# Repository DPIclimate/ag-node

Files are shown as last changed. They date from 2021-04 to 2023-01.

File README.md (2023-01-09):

<h2 align="center">
    Agriculture Node
</h2>
<p align="center">
  <a href="#about">About</a> •
  <a href="#schematic">Schematic</a> •
  <a href="#protocol / algorithm">Protocol</a> •
  <a href="#firmware docs">Docs</a> •
  <a href="#license">License</a>
</p>

<p align="center">
  <a href="https://dpiclimate.github.io/ag-node">
    
  </a>
</p>



## About

The agriculture node (ag-node) is an automatic multi-weigh-station for measuring the live-weight of sheep  in remote locations. The station can be situated against a trough for which sheep weights will be recorded as they access feed or water. An in-built LoRaWAN radio sends data (containing live-weight information) back to a local gateway and onto the end user. Additional interfaces are provided, including; SDI-12, I<sub>2</sub>C and OneWire to allow for various sensors to be connected to the device (such as trough level sensors, temperature monitors etc.).

## Schematic

The devices schematic can be found at: [schematic.pdf](https://github.com/DPIclimate/ag-node/blob/master/figures/schematic.pdf)

Basic components are summarised in the below image. Where A is the analog-to-digital converter, B is the LoRaWAN communication infrastructure and C is the peripheral sensor connectors (I<sub>2</sub>C, OneWire and SDI-12).

<div align="middle"> 
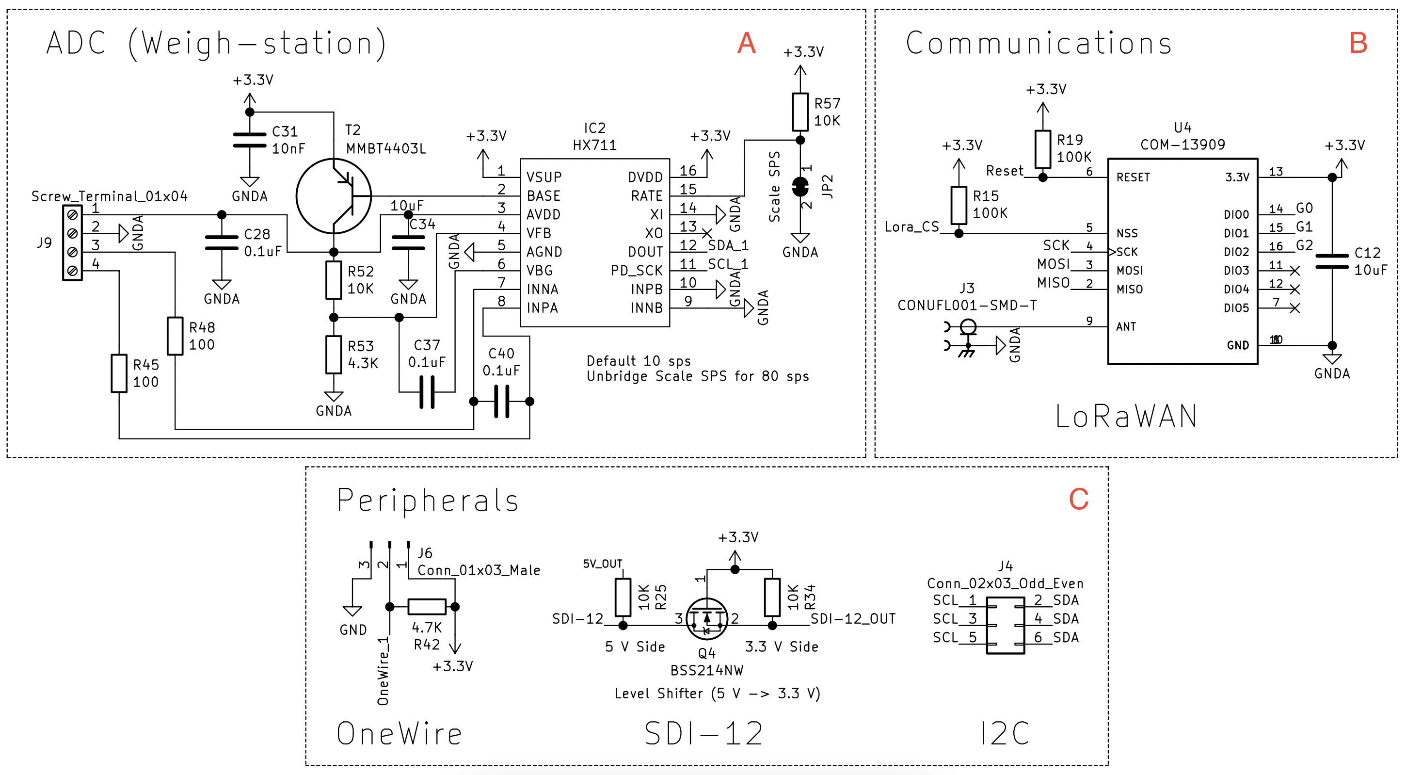
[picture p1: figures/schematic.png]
	
</div>

## Protocol / Algorithm

As the device operates autonomously (sheep are weighed in an unsupervised manner) an algorithm to capture the maximum stable weight (and an error representation) is provided.

The protocol is explained below and a visual representation is provided.

1. A weight is captured (triggered by a sheep stepping on a scale) consisting of a time-series of weights while the sheep is on the platform

2. This time-series data is sliced into groups of 5 values

3. The slope between the first and last value is calculated (where values < 0.1) are discarded as they represent unstable weights

4. The Root Mean Square Error (RMSE) of the fitted line is calculated

5. The average of the 5 points are taken

6. An evaluation of the new weight is made against previous slices (see figure below under the Method `Evaluate` for an equation that represents this)

<div align="middle"> 
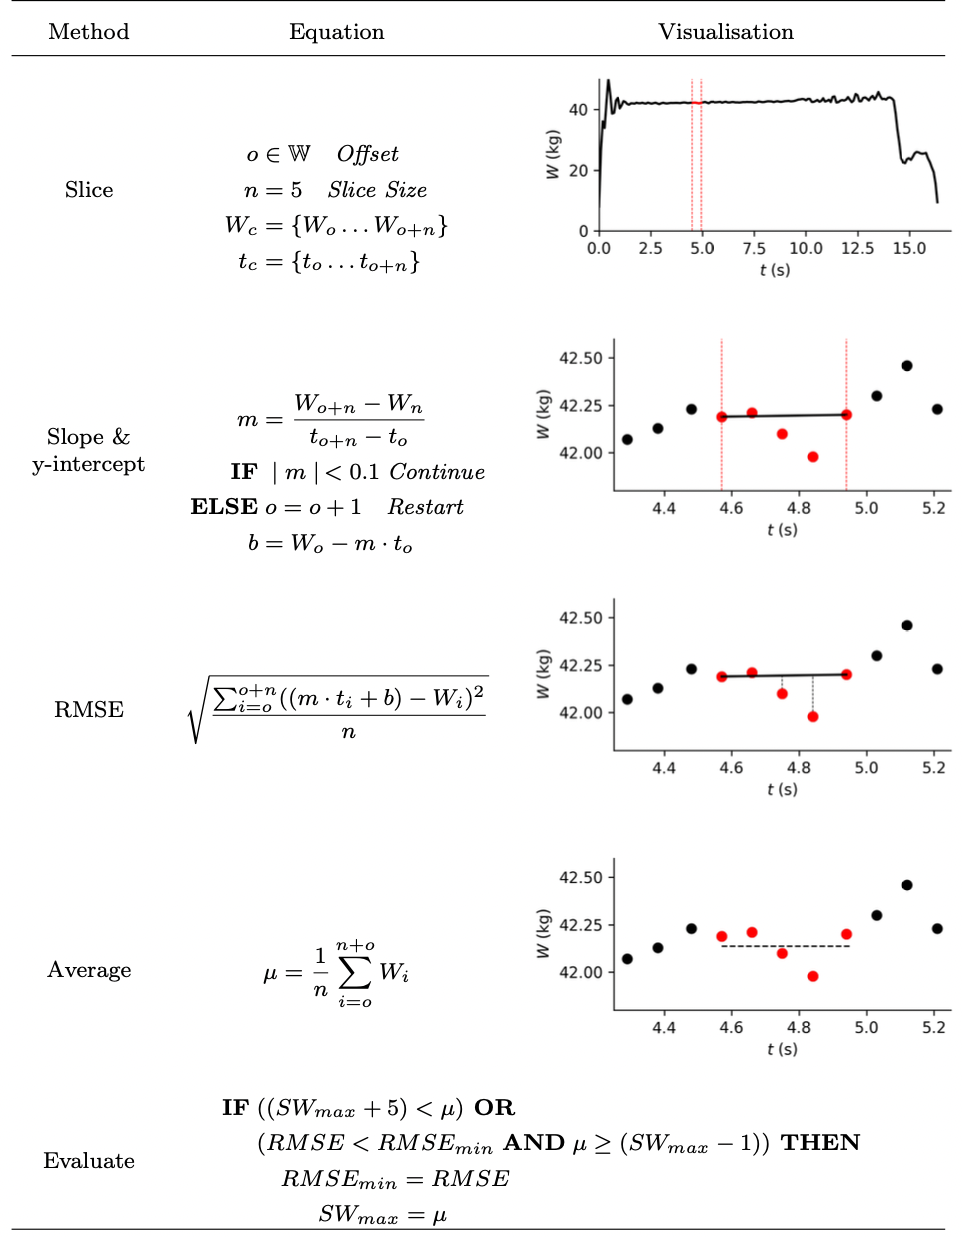
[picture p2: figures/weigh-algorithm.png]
	
</div>

## Firmware Docs

Firmware documentation can be found [here](https://dpiclimate.github.io/ag-node)

An illustration of the devices operations can be found below:

<div align="middle"> 
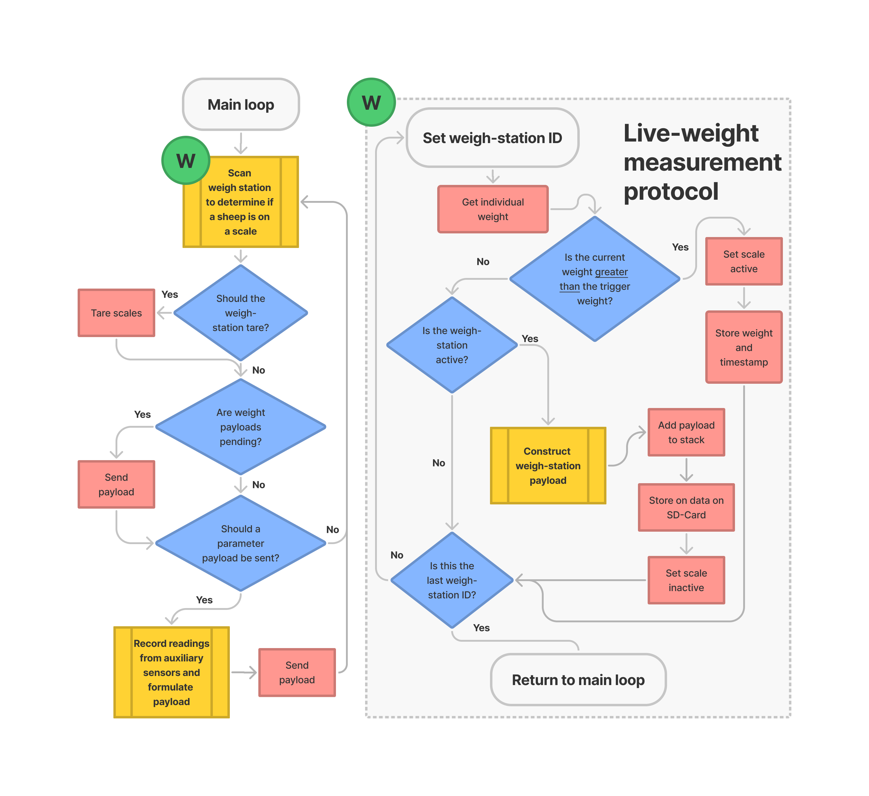
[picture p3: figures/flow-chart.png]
	
</div>

## License

Ag-node is MIT licensed, as found in the [LICENSE](https://github.com/DPIclimate/ag-node/blob/master/LICENSE) file.

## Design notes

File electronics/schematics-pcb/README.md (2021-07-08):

## Version 0.3
- Uses Teensy 3.6 as mainboard controller (run at a low clock speed) and defaults to sleep
- Has 3 weigh station ports (controlled by a HX711 and a ATMega328) 
- ATMega328's have interrupts connected to the teensy to wake it up when they want to transfer some data (over I2C)
- Single lorawan module (connected to teensy, can sleep when not in use)
- Designed to be a low-power device with multiple processors for asynchronous readings

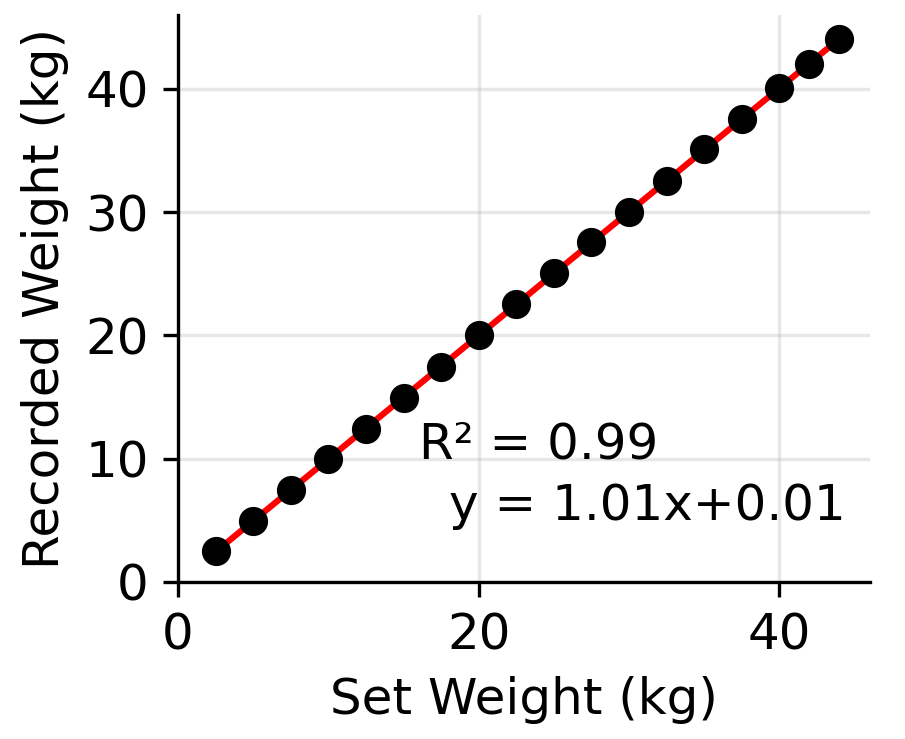
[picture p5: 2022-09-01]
figures/linearity.png

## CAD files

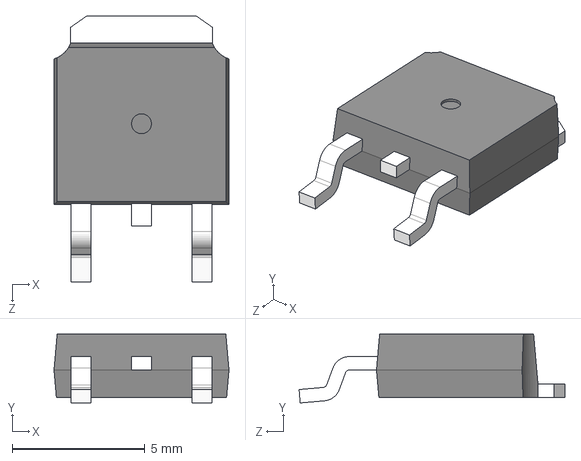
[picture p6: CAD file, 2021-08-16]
electronics/additionalParts/AOD417/AOD417.step
6.60 x 2.60 x 10.0 mm

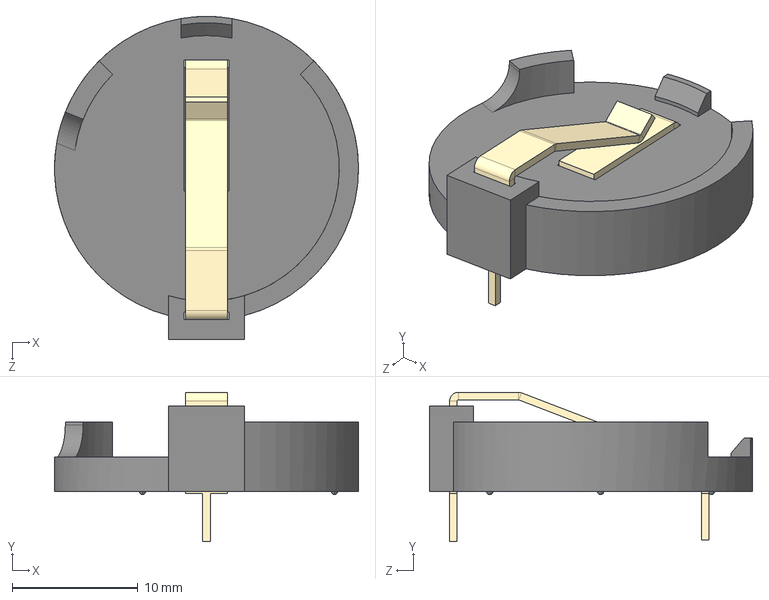
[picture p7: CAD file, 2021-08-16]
electronics/additionalParts/BH32T-C-G/BH32T-C-G.step
24.1 x 11.9 x 25.7 mm

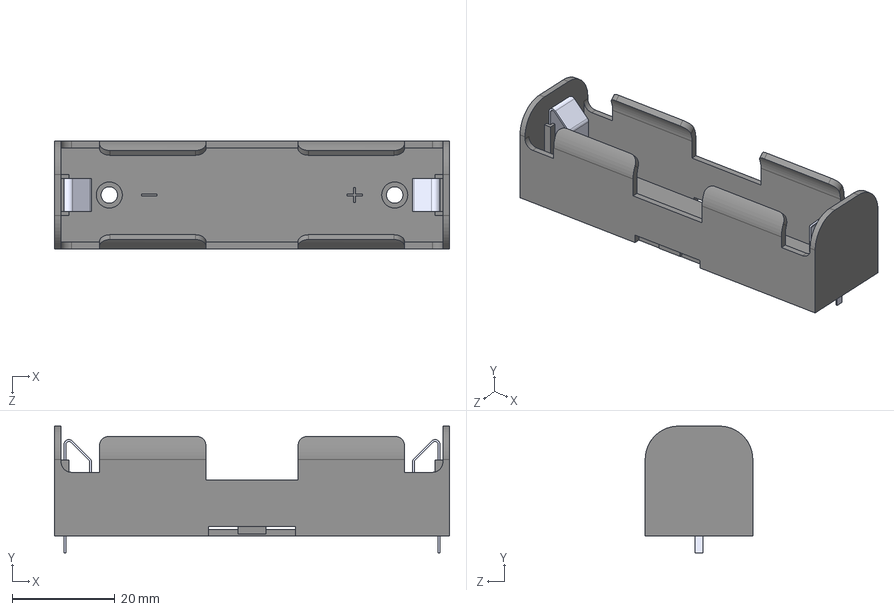
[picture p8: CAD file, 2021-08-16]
electronics/additionalParts/BK-18650-PC2/BK-18650-PC2.step
77.0 x 24.7 x 21.0 mm

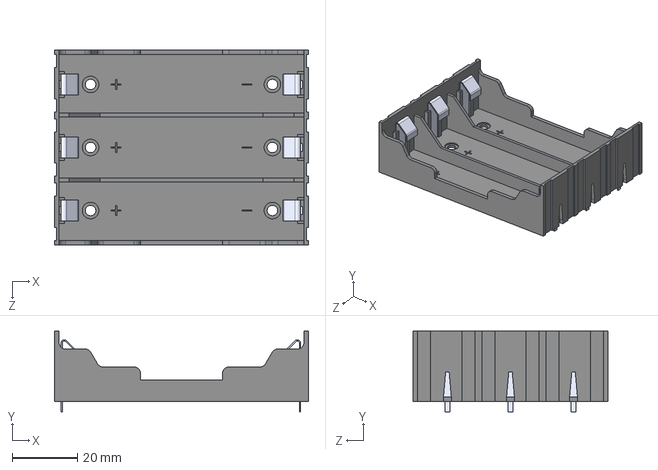
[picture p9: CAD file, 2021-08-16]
electronics/additionalParts/BK-18650-PC6/BK-18650-PC6.step
77.7 x 24.7 x 59.7 mm

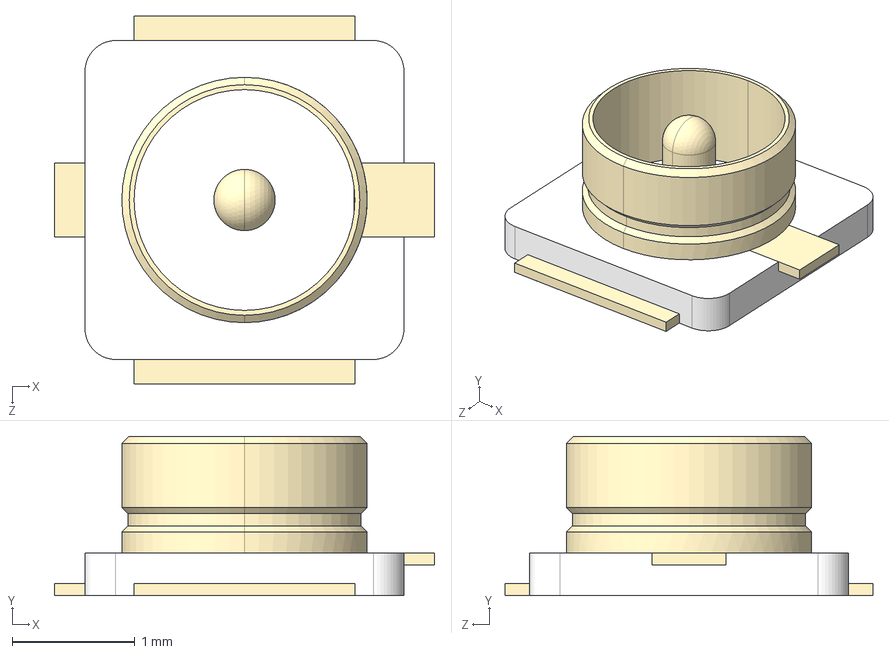
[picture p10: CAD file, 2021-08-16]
electronics/additionalParts/CONUFL001-SMD-T/CONUFL001-SMD-T.step
3.10 x 1.30 x 3.00 mm

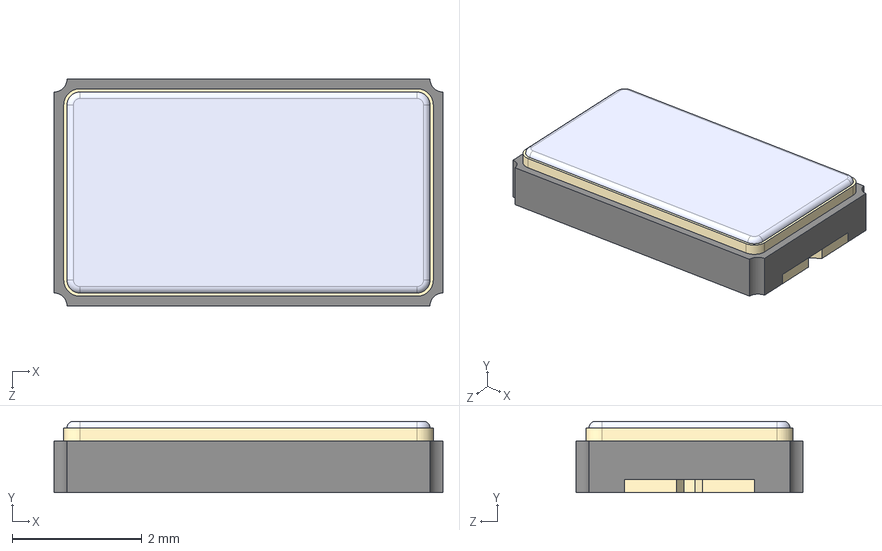
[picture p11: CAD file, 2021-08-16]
electronics/additionalParts/ECS-200-20-23A-EN-TR/ECS-200-20-23A-EN-TR.step
6.00 x 1.10 x 3.50 mm

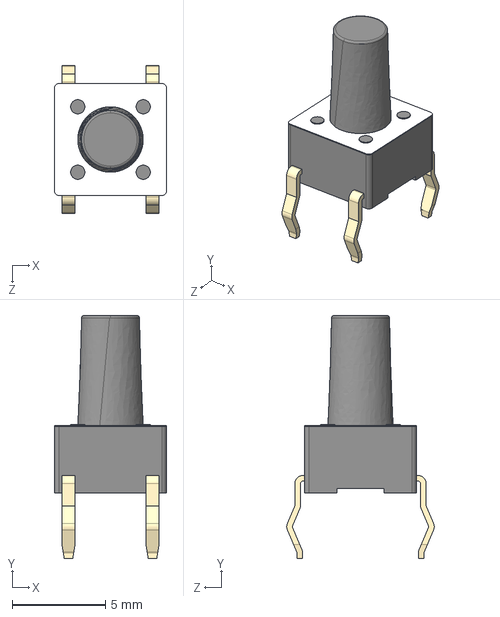
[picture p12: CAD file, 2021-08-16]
electronics/additionalParts/FSM8JH/FSM8JH.step
5.99 x 13.0 x 7.90 mm

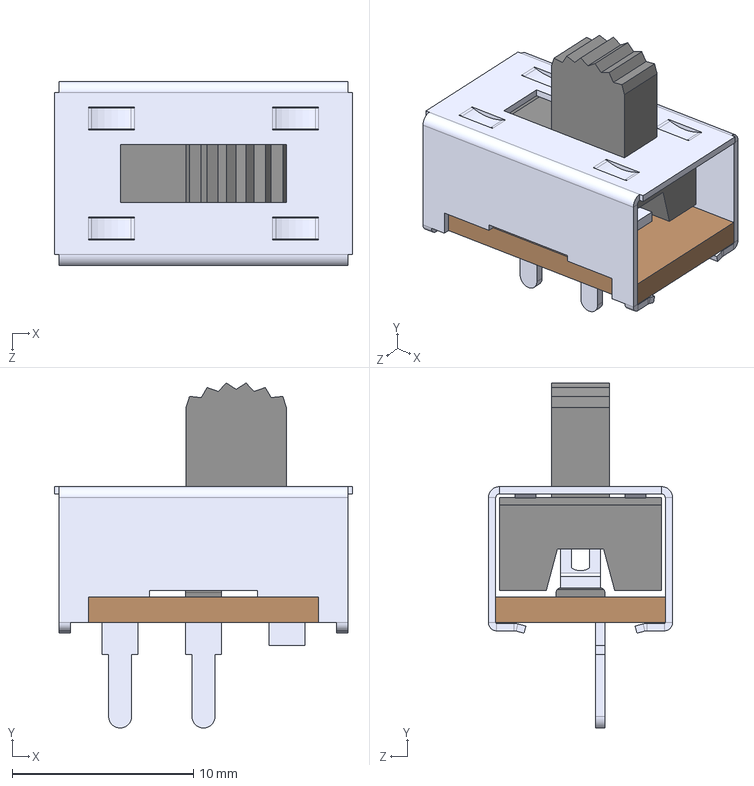
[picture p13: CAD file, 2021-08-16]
electronics/additionalParts/GF-123-0054/GF-123-0054.step
16.5 x 19.0 x 10.2 mm

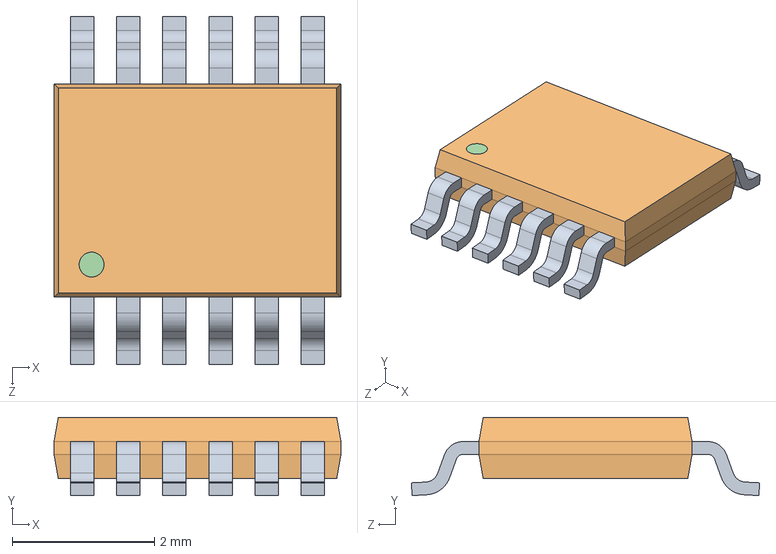
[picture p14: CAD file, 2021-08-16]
electronics/additionalParts/LT3652IMSETRPBF/LT3652IMSETRPBF.step
4.04 x 1.10 x 4.90 mm

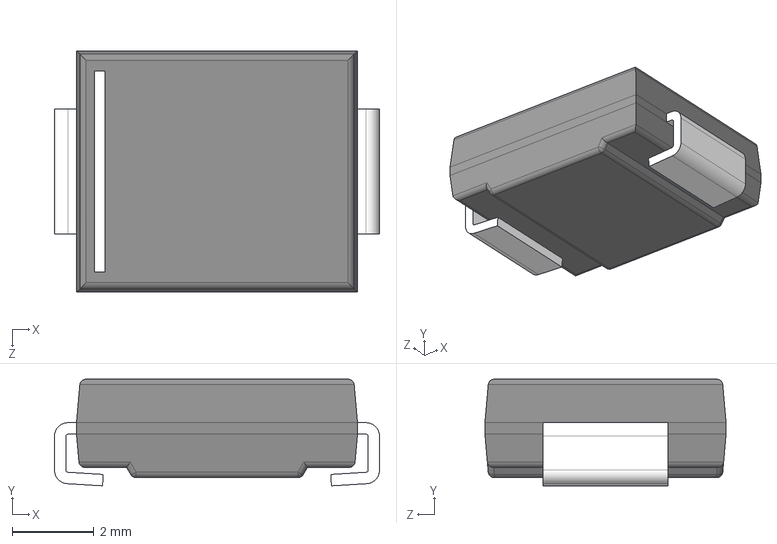
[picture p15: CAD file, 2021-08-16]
electronics/additionalParts/MBRS340/MBRS340.step
7.95 x 2.61 x 5.90 mm

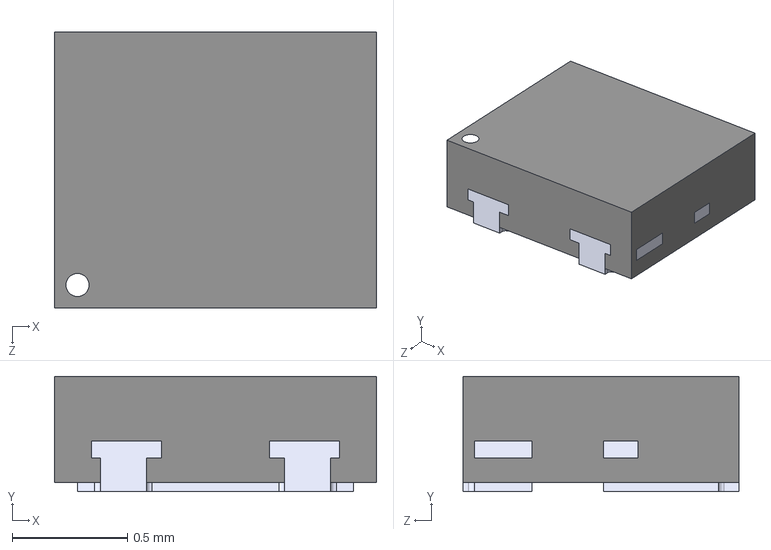
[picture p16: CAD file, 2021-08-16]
electronics/additionalParts/MMBT4403L/MMBT4403L.step
1.40 x 0.5 x 1.20 mm

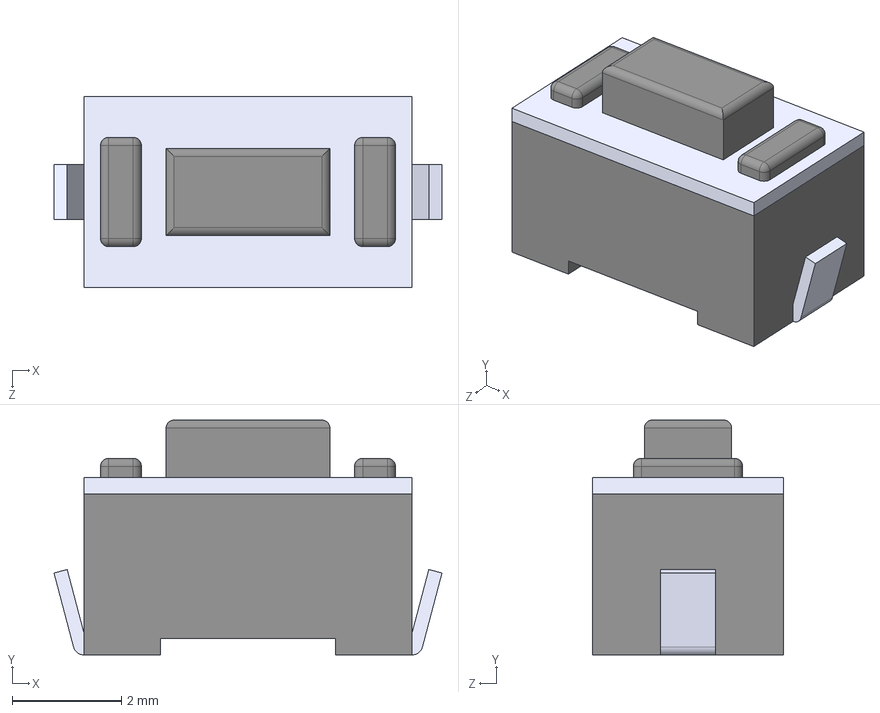
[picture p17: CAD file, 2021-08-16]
electronics/additionalParts/PTS636_SM43J_SMTR_LFS/PTS636_SM43J_SMTR_LFS.step
7.10 x 4.30 x 3.50 mm

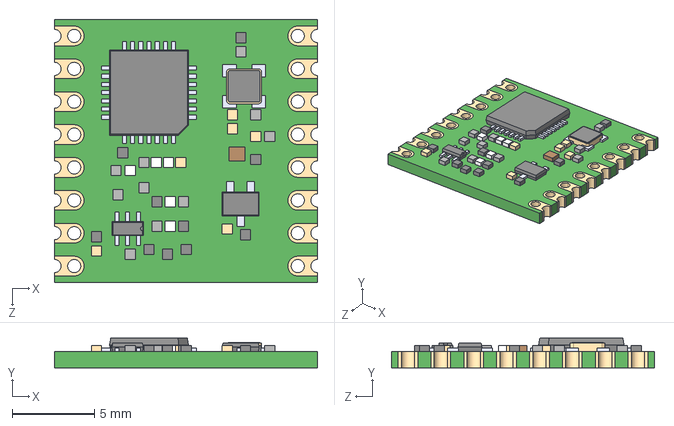
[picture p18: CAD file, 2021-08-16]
electronics/additionalParts/RFM69HCW/COM-13909.step
16.0 x 1.80 x 16.0 mm

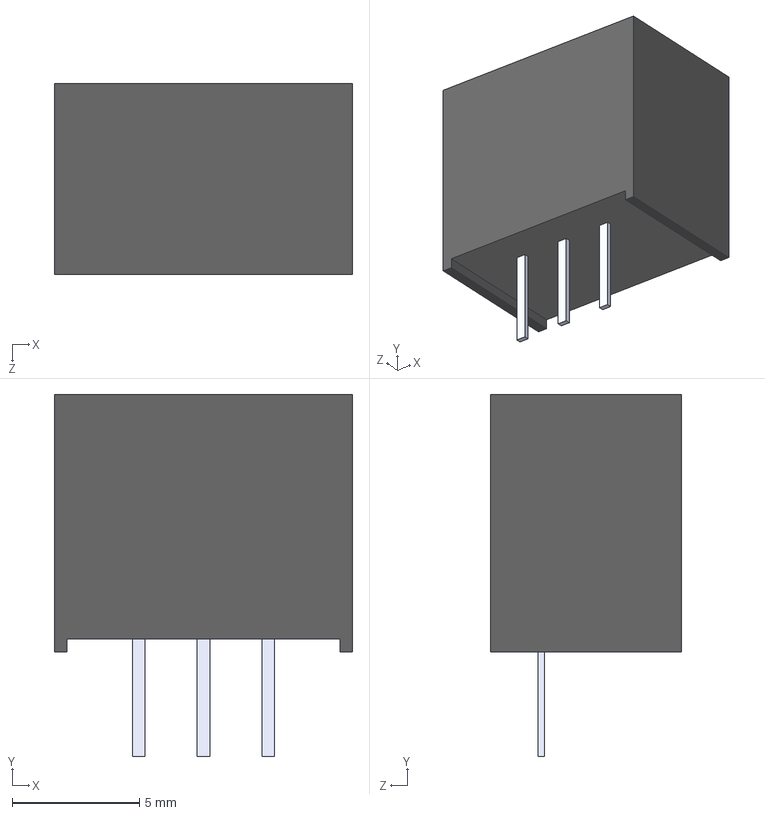
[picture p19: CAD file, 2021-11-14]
electronics/additionalParts/TSR_1-2450/TSR_1-2450.step
11.7 x 14.2 x 7.50 mm

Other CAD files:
electronics/additionalParts/TXB0104D/TXB0104D.step
electronics/additionalParts/L101011MS02Q/L101011MS02Q.step
electronics/additionalParts/TPS73633DBVT/TPS73633DBVT.step

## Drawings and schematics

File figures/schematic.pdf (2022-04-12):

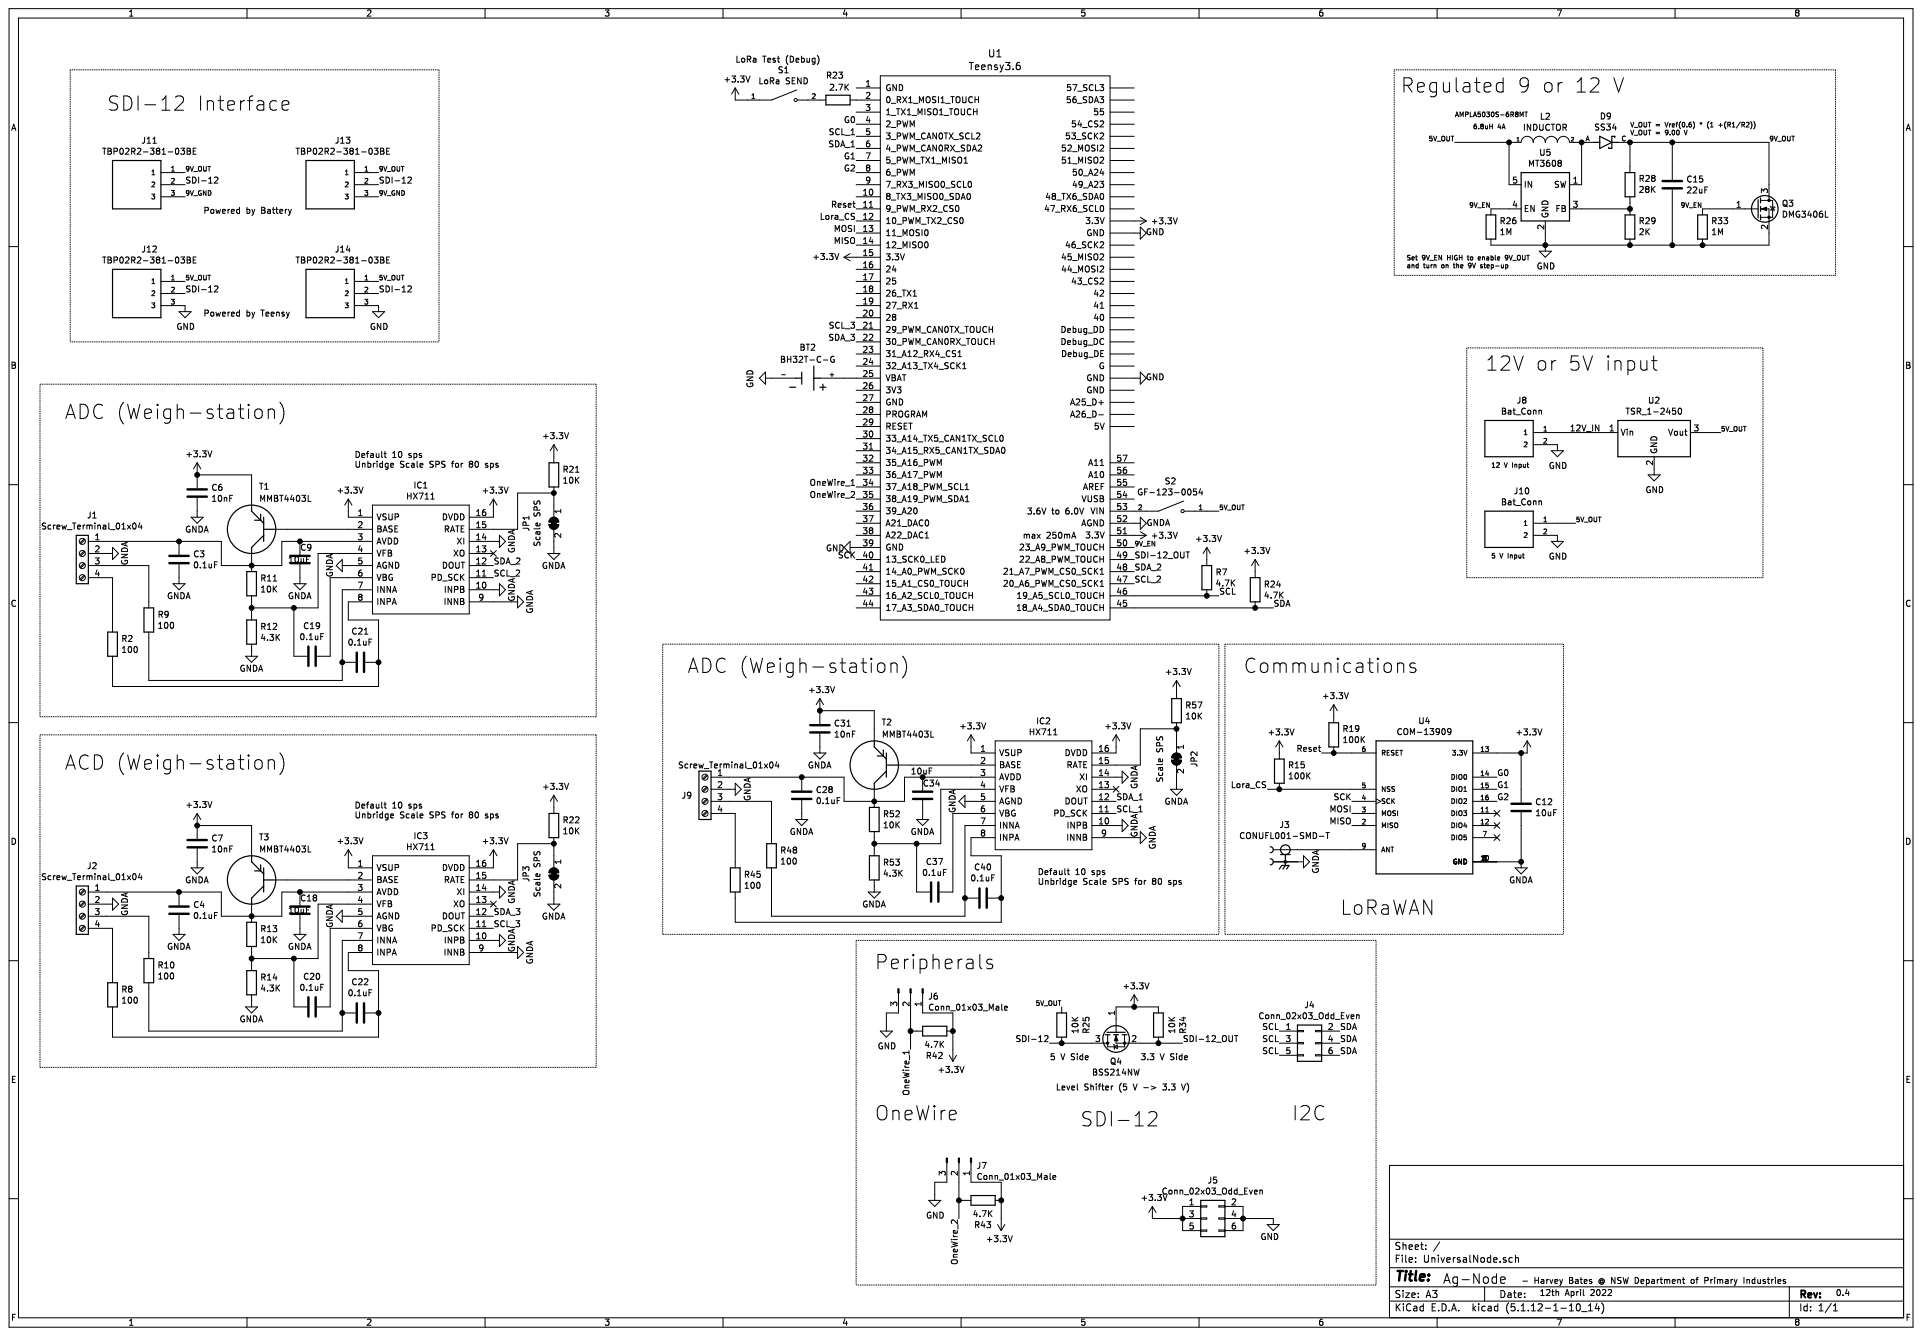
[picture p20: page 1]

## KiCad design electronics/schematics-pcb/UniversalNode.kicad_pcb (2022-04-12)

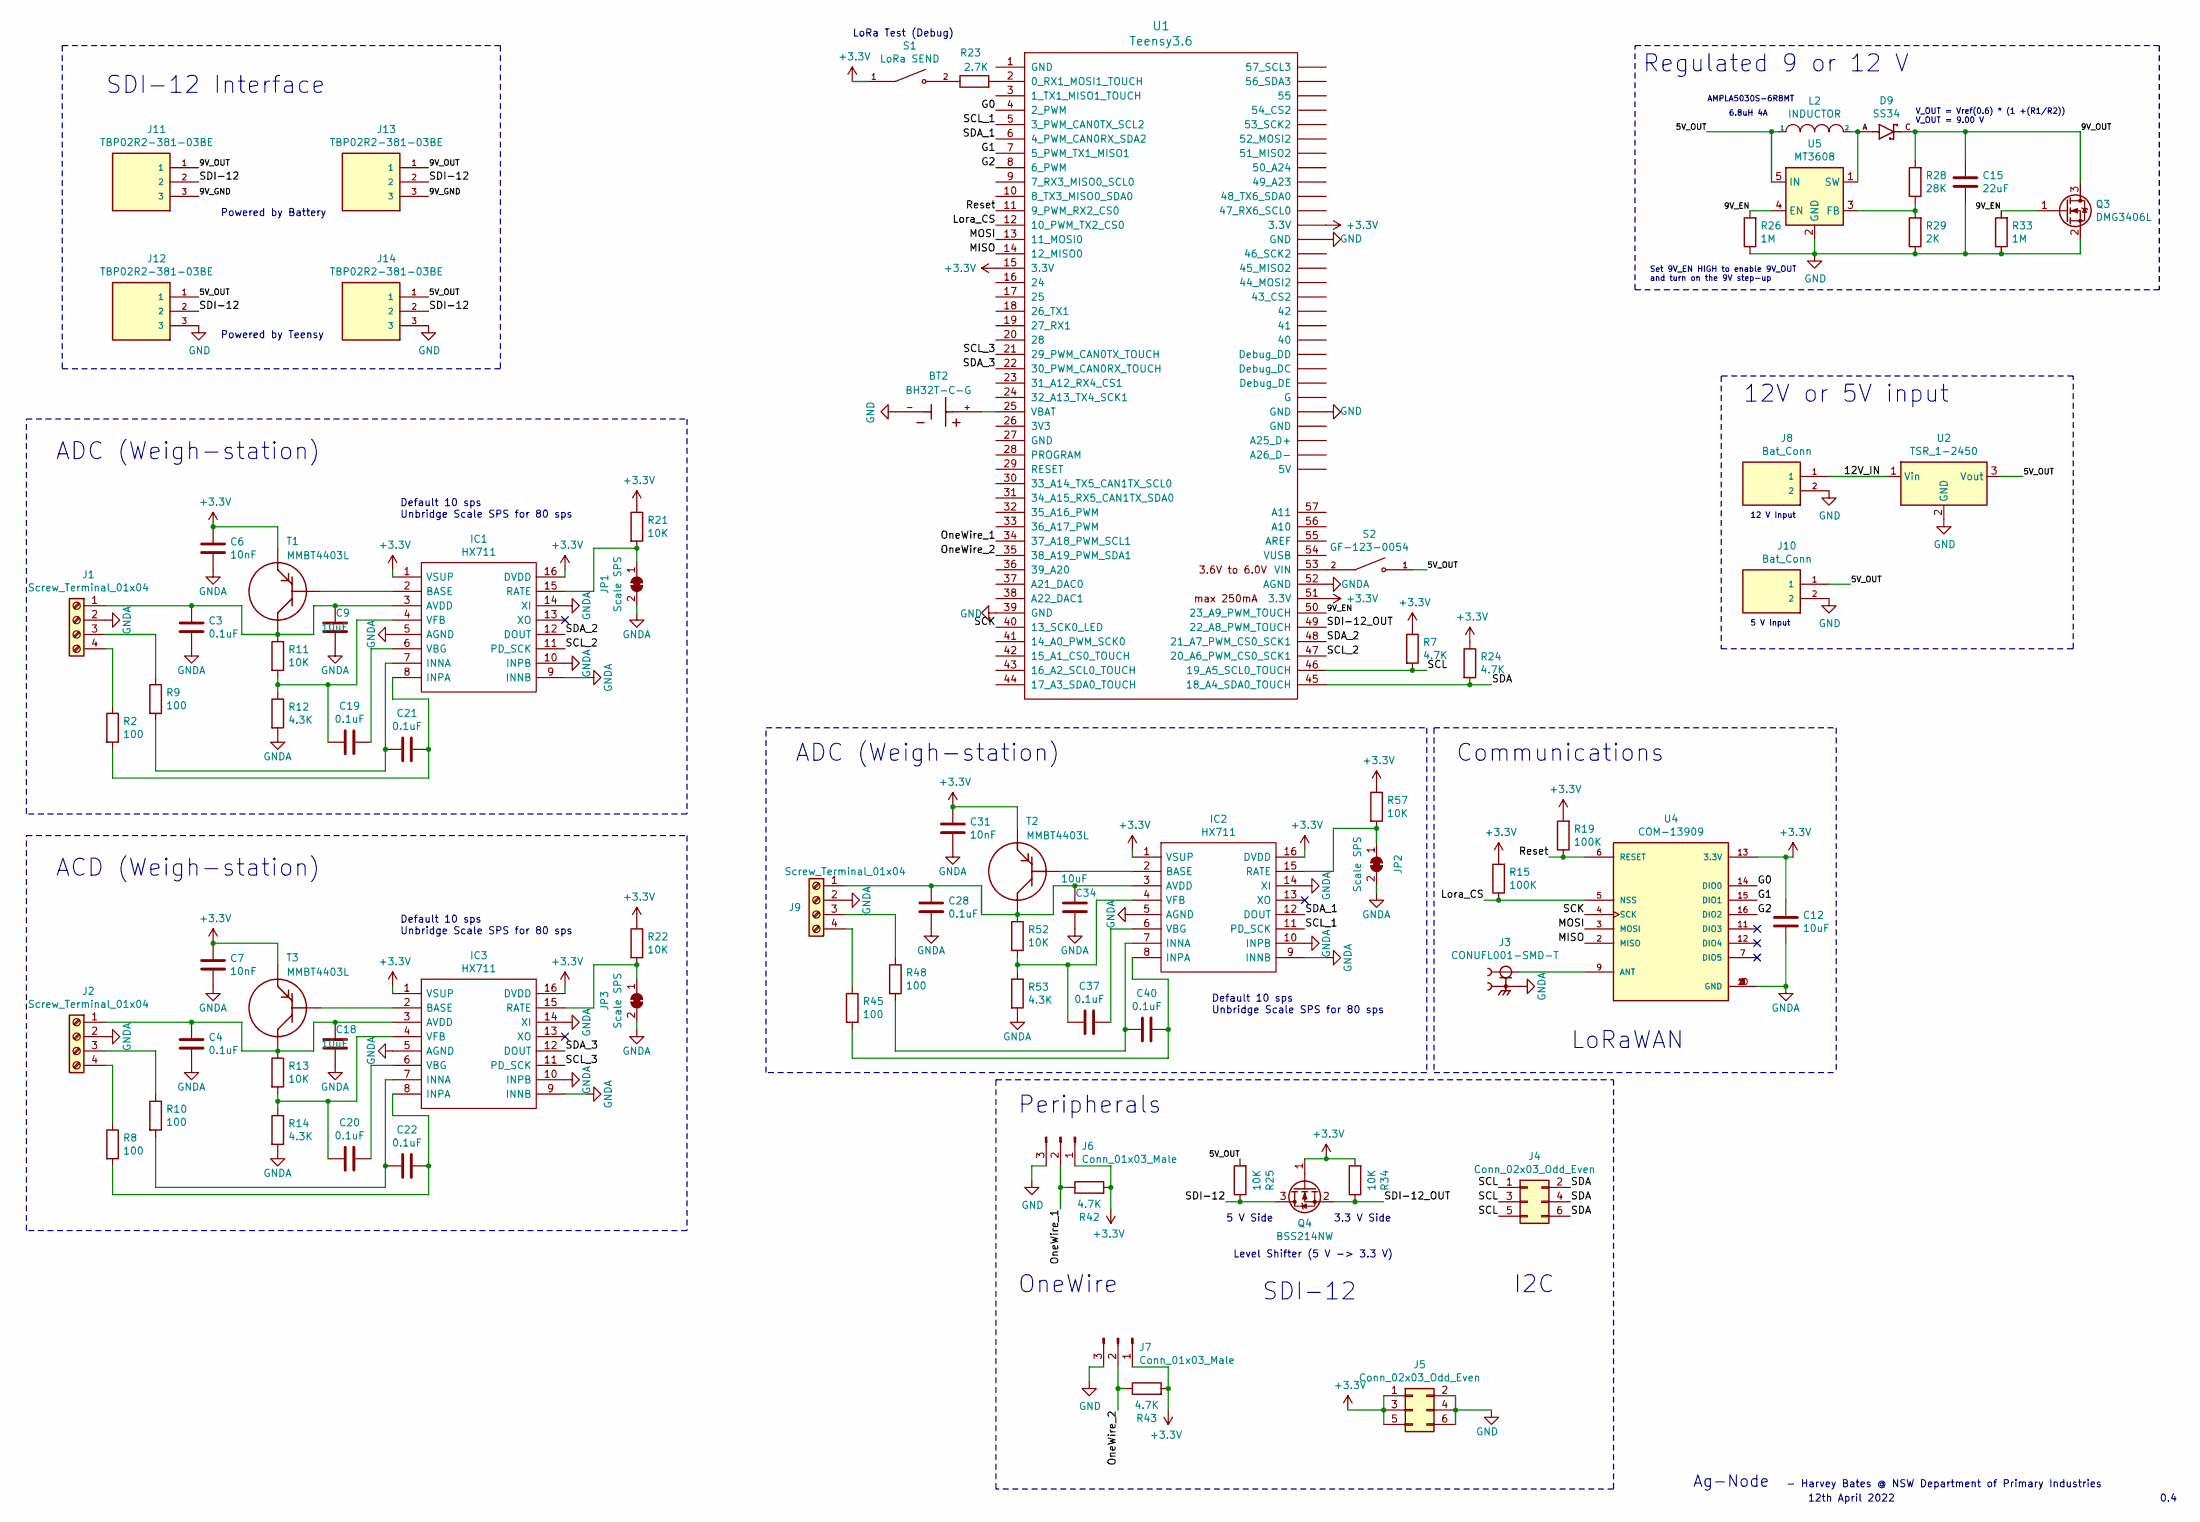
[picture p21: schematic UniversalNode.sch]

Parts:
BT2: BH32T-C-G; BAT_BH32T-C-G; PARTREV B
C3, C4, C19, C20, C21, C22, C28, C37, C40: 0.1uF; C_0805_2012Metric
C6, C7, C31: 10nF; C_0805_2012Metric
C9, C12, C18, C34: 10uF; CP_Elec_5x5.4
C15: 22uF; CP_Elec_6.3x5.9
D9: SS34; DIOM7959X265N; PARTREV 31 Aug 2016
IC1, IC2, IC3: HX711; SOIC127P600X160-16N; Manufacturer_Part_Number HX711
J1, J2, J9: Screw_Terminal_01x04; OSTOQ043250
J3: CONUFL001-SMD-T; LINX_CONUFL001-SMD-T; PARTREV B
J4, J5: Conn_02x03_Odd_Even; PinSocket_2x03_P2.54mm_Vertical
J6, J7: Conn_01x03_Male; PinSocket_1x03_P2.54mm_Vertical
J8, J10: Bat_Conn; 102-6492-ND‎
J11, J12, J13, J14: TBP02R2-381-03BE; CUI_TBP02R2-381-03BE
JP1, JP2, JP3: Scale SPS; SolderJumper-2_P1.3mm_Bridged_Pad1.0x1.5mm
L2: INDUCTOR; AMPLA5030S-6R8MT
Q3: DMG3406L; SOT-23
Q4: BSS214NW; SOT-323_SC-70
R2, R8, R9, R10, R45, R48: 100; R_0805_2012Metric
R7, R24, R42, R43: 4.7K; R_0805_2012Metric
R11, R13, R21, R22, R25, R34, R52, R57: 10K; R_0805_2012Metric
R12, R14, R53: 4.3K; R_0805_2012Metric
R15, R19: 100K; R_0805_2012Metric
R23: 2.7K; R_0805_2012Metric
R26, R33: 1M; R_0805_2012Metric
R28: 28K; R_0805_2012Metric
R29: 2K; R_0805_2012Metric
S1: LoRa SEND; SW_PTS636_SM43J_SMTR_LFS; PARTREV 27 mar 19
S2: GF-123-0054; SW_GF-123-0054; PARTREV May 20, 2003
T1, T2, T3: MMBT4403L; SOT23
U1: Teensy3.6; Teensy35_36
U2: TSR_1-2450; Converter_DCDC_TRACO_TSR-1_THT
U4: COM-13909; MOD_COM-13909
U5: MT3608; SOT-23-6

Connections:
+3V3: C6.1, C7.1, C12.1, C31.1, IC1.1 (VSUP), IC1.16 (DVDD), IC2.1 (VSUP), IC2.16 (DVDD), IC3.1 (VSUP), IC3.16 (DVDD), J5.1, J5.3, J5.5, J6.1, J7.1, Q4.1 (G), R7.1, R15.2, R19.2, R21.1, R22.1, R24.1, R34.2, R42.2, R43.2, R57.1, S1.1, T1.2, T2.2, T3.2, U1.15 (3.3V), U1.51 (3.3V), U1.~ (3.3V), U4.13 (3.3V)
/5V_OUT: J10.1, J12.1, J14.1, L2.1, R25.2, S2.1, U2.3 (Vout), U5.5 (IN)
/9V_EN: Q3.1 (G), R26.2, R33.2, U1.50 (23_A9_PWM_TOUCH), U5.4 (EN)
/9V_GND: J11.3, J13.3
/9V_OUT: C15.1, D9.C, J11.1, J13.1, Q3.3 (D), R28.2
/12V_IN: J8.1, U2.1 (Vin)
/G0: U1.4 (2_PWM), U4.14 (DIO0)
/G1: U1.7 (5_PWM_TX1_MISO1), U4.15 (DIO1)
/G2: U1.8 (6_PWM), U4.16 (DIO2)
/Lora_CS: R15.1, U1.12 (10_PWM_TX2_CS0), U4.5 (NSS)
/MISO: U1.14 (12_MISO0), U4.2 (MISO)
/MOSI: U1.13 (11_MOSI0), U4.3 (MOSI)
/OneWire_1: J6.2, R42.1, U1.34 (37_A18_PWM_SCL1)
/OneWire_2: J7.2, R43.1, U1.35 (38_A19_PWM_SDA1)
/Reset: R19.1, U1.11 (9_PWM_RX2_CS0), U4.6 (RESET)
/SCK: U1.40 (13_SCK0_LED), U4.4 (SCK)
/SCL: J4.1, J4.3, J4.5, R7.2, U1.46 (19_A5_SCL0_TOUCH)
/SCL_1: IC2.11 (PD_SCK), U1.5 (3_PWM_CAN0TX_SCL2)
/SCL_2: IC1.11 (PD_SCK), U1.47 (20_A6_PWM_CS0_SCK1)
/SCL_3: IC3.11 (PD_SCK), U1.21 (29_PWM_CAN0TX_TOUCH)
/SDA: J4.2, J4.4, J4.6, R24.2, U1.45 (18_A4_SDA0_TOUCH)
/SDA_1: IC2.12 (DOUT), U1.6 (4_PWM_CAN0RX_SDA2)
/SDA_2: IC1.12 (DOUT), U1.48 (21_A7_PWM_CS0_SCK1)
/SDA_3: IC3.12 (DOUT), U1.22 (30_PWM_CAN0RX_TOUCH)
/SDI-12: J11.2, J12.2, J13.2, J14.2, Q4.3 (D), R25.1
/SDI-12_OUT: Q4.2 (S), R34.1, U1.49 (22_A8_PWM_TOUCH)
GND: BT2.-, C15.2, J5.2, J5.4, J5.6, J6.3, J7.3, J8.2, J10.2, J12.3, J14.3, Q3.2 (S), R26.1, R29.1, R33.1, U1.39 (GND), U1.~ (3.3V), U2.2 (GND), U5.2 (GND)
GNDA: C3.2, C4.2, C6.2, C7.2, C9.2, C12.2, C18.2, C28.2, C31.2, C34.2, IC1.5 (AGND), IC1.9 (INNB), IC1.10 (INPB), IC1.14 (XI), IC2.5 (AGND), IC2.9 (INNB), IC2.10 (INPB), IC2.14 (XI), IC3.5 (AGND), IC3.9 (INNB), IC3.10 (INPB), IC3.14 (XI), J1.2, J2.2, J3.2, J3.3, J9.2, JP1.2 (B), JP2.2 (B), JP3.2 (B), R12.2, R14.2, R53.2, U1.52 (AGND), U4.1 (GND), U4.8 (GND), U4.10 (GND)
unnamed: BT2.+, U1.25 (VBAT)
unnamed: C3.1, C9.1, IC1.3 (AVDD), J1.1, R11.1, T1.3
unnamed: C4.1, C18.1, IC3.3 (AVDD), J2.1, R13.1, T3.3
unnamed: C19.1, IC1.6 (VBG)
unnamed: C19.2, IC1.4 (VFB), R11.2, R12.1
unnamed: C20.1, IC3.6 (VBG)
unnamed: C20.2, IC3.4 (VFB), R13.2, R14.1
unnamed: C21.1, IC1.7 (INNA), R9.2
unnamed: C21.2, IC1.8 (INPA), R2.2
unnamed: C22.1, IC3.7 (INNA), R10.2
unnamed: C22.2, IC3.8 (INPA), R8.2
unnamed: C28.1, C34.1, IC2.3 (AVDD), J9.1, R52.1, T2.3
unnamed: C37.1, IC2.6 (VBG)
unnamed: C37.2, IC2.4 (VFB), R52.2, R53.1
unnamed: C40.1, IC2.7 (INNA), R48.2
unnamed: C40.2, IC2.8 (INPA), R45.2
unnamed: D9.A, L2.2, U5.1 (SW)
unnamed: IC1.2 (BASE), T1.1
unnamed: IC1.15 (RATE), JP1.1 (A), R21.2
unnamed: IC2.2 (BASE), T2.1
unnamed: IC2.15 (RATE), JP2.1 (A), R57.2
unnamed: IC3.2 (BASE), T3.1
unnamed: IC3.15 (RATE), JP3.1 (A), R22.2
unnamed: J1.3, R9.1
unnamed: J1.4, R2.1
unnamed: J2.3, R10.1
unnamed: J2.4, R8.1
unnamed: J3.1, U4.9 (ANT)
unnamed: J9.3, R48.1
unnamed: J9.4, R45.1
unnamed: R23.1, S1.2
unnamed: R23.2, U1.2 (0_RX1_MOSI1_TOUCH)
unnamed: R28.1, R29.2, U5.3 (FB)
unnamed: S2.2, U1.53 (VIN)

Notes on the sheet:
Ag-Node
12th April 2022
- Harvey Bates @ NSW Department of Primary Industries
0.4
Powered by Battery
Powered by Teensy
SDI-12 Interface
ACD (Weigh-station)
Default 10 sps Unbridge Scale SPS for 80 sps
ADC (Weigh-station)
5 V Input
12V or 5V input
12 V Input
Set 9V_EN HIGH to enable 9V_OUT and turn on the 9V step-up
Regulated 9 or 12 V
V_OUT = Vref(0.6) * (1 +(R1/R2)) V_OUT = 9.00 V
AMPLA5030S-6R8MT
6.8uH 4A
LoRa Test (Debug)
OneWire
I2C
SDI-12
Level Shifter (5 V -> 3.3 V)
5 V Side
3.3 V Side
Peripherals
LoRaWAN
Communications

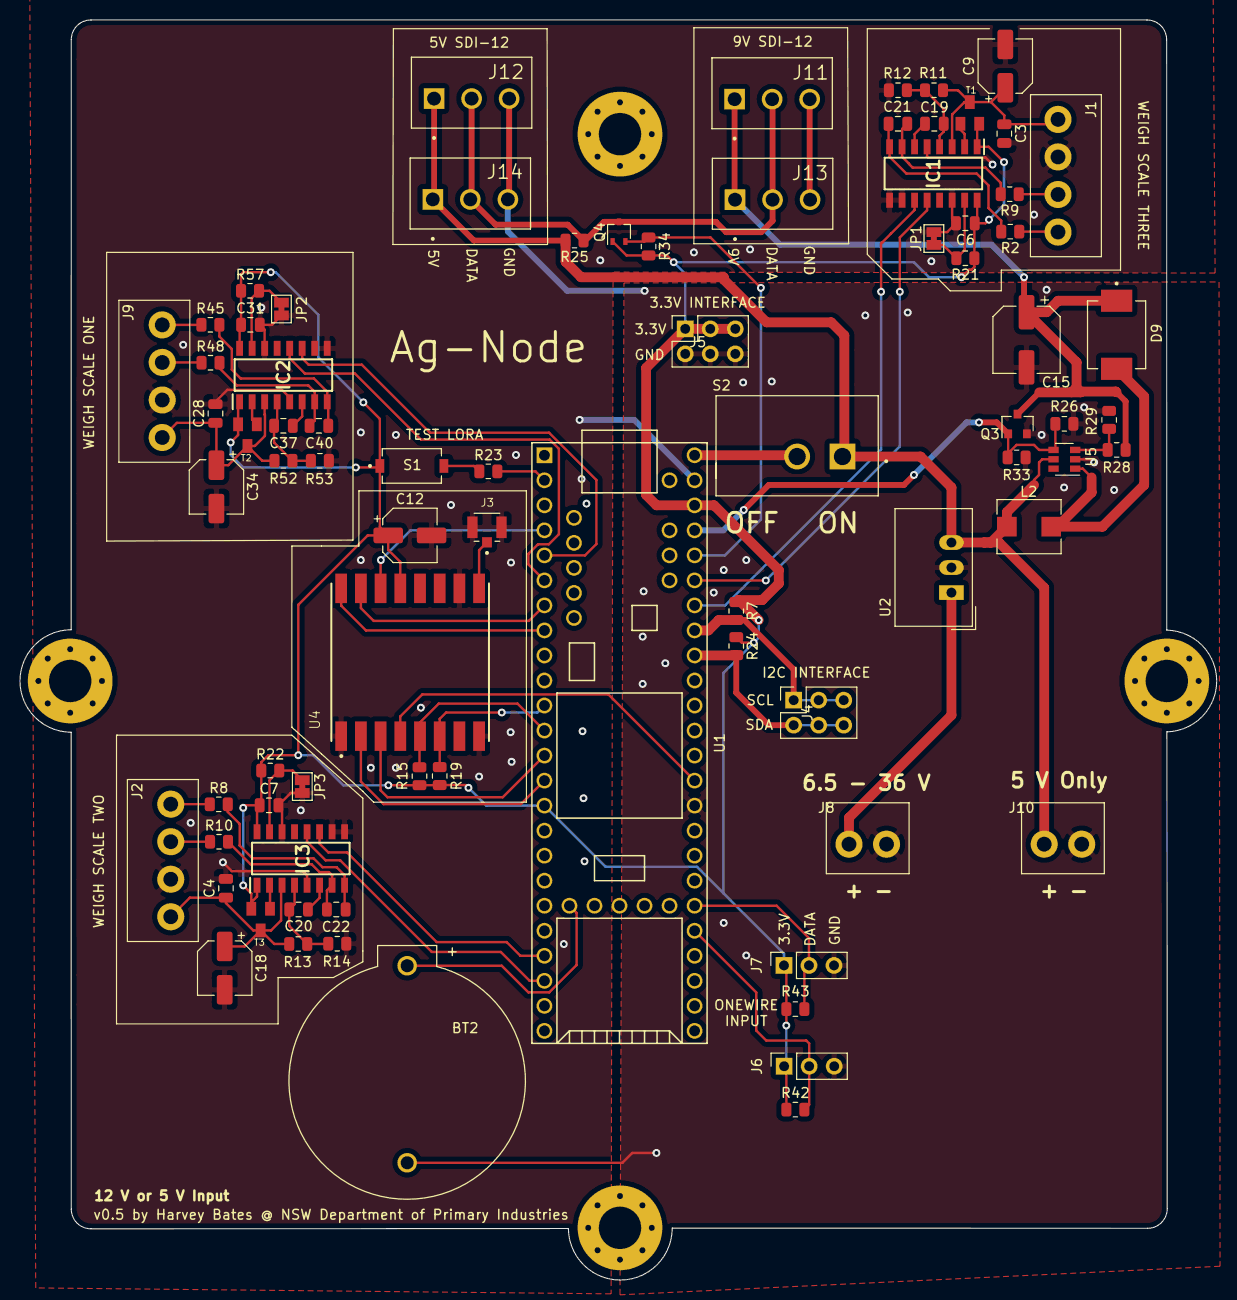
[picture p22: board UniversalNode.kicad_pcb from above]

Board: 2 copper layers, 121.5 x 127.9 mm, 79 parts (0 on the bottom side), 62 nets.

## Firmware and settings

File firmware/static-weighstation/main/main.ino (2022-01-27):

// Local imports
#ifdef ENABLE_LORAWAN
  #include "lora.h"
#endif
#include "sensors.h"
#include "memory.h"

#ifdef LOW_POWER
  #include <Snooze.h>
  SnoozeUSBSerial usb;
  SnoozeAlarm alarm;
  SnoozeBlock sleepConfig(usb, alarm);
#endif

// Temperature related setup
OneWire oneWire(ONE_WIRE_BUS);
DallasTemperature sensors(&oneWire);

bool sensorPayload = true; // Has payload been sent over LoRa
uint8_t tareScales = 0; // Tare scales after 255 readings

// Time related variables for distributing LoRaWAN paylaods
uint32_t timer = 0;
uint32_t lastMessage = 0;
uint32_t messageSpacing = 1000 * 60; // ms

WeighStation weighStation; // Create weighstation object

void setup() {
  Serial.begin(57600);
  
  #ifdef DEBUG
    while(!Serial) delay(100);
  #endif

  pinMode(LED_BUILTIN, OUTPUT);
  
  #ifdef ENABLE_LORAWAN
    Lora::init();
    while(!Lora::check_state()) {
      os_runloop_once();
    }
  #endif

  #ifdef LOW_POWER
    // Send a sensor payload every night at 30 minute intervals
    alarm.setRtcTimer(0, 30, 0);
  #endif

  // Setup classes
  RealTimeClock::init();
  Temperature::init(sensors);
  Monitoring::init();
  weighStation.init();
  Memory::init();

  watchDogReset();
}


void watchDogReset(){
  noInterrupts();
  WDOG_REFRESH = 0xA602;
  WDOG_REFRESH = 0xB480;
  interrupts();
}


void loop() {
  
  // Keep track of when the last message was sent
  timer = millis() - lastMessage;

  // ======== Weight Payload ========
  
  // Scan scales to see if animal is on scale
  weighStation.scan();

  // Reset scale to zero (every 255 readings) - providing there isn't an animal on scale
  if(tareScales == 255 && !weighStation.check_state()) {
    WeighStation::tare_scales();
    tareScales++;
  } else tareScales++;

  // Send stored weigh payloads over LoRa
  if(!weighStation.check_state() && weighStation.payloadPos != 0 && timer >= messageSpacing) {
    weighStation.forward_payload();
    // Reset timer - prevents slow LoRa transimission
    lastMessage = millis();
    // Reset scales timer (just incase there is now an animal on scale)
    tareScales = 0; 
  }

  // Small delay to prevent high current usage 
  if(!weighStation.check_state()) {
    delay(200);
  }

  watchDogReset(); // Reset watchdog timer

  // ======== Sensor Payload ========
  
  // Reset sensor payload send state - prevents multiple packets
  if(timer >= messageSpacing && sensorPayload) sensorPayload = false;

  // Every 5 min send sensor payload (monitoring and temperature)
  if(minute() % 5 == 0 && !sensorPayload) {
    #ifdef ENABLE_LORAWAN
      int8_t* sensorsPayload = Sensors::construct_payload();
      Lora::request_send(sensorsPayload, 2);

      while(!Lora::check_state()) {
        os_runloop_once();
      }
      Serial.println("[SENSORS]: Payload sent.");
      sensorPayload = true;
    #endif
    // Reset timer - preventing slow LoRa transmission
    lastMessage = millis();
    // Reset scales timer - just incase there is now an animal on scale
    tareScales = 0; 
  }

  // ======== Sleep (Night-time) ========
  
  #ifdef LOW_POWER
    // Between 6 pm and 6 am
    while(hour() >= 18 || hour() < 6) {
      weighStation.sleep();
      int who;
      who = Snooze.sleep(sleepConfig);
      // Send a payload
      int8_t* sensorsPayload = Sensors::construct_payload();
      #ifdef ENABLE_LORAWAN
        Lora::request_send(sensorsPayload, 2); 
        while(!Lora::check_state()){
          os_runloop_once();
        }
      #endif
      weighStation.wakeup();
    }
  #endif
}



#ifdef __cplusplus
extern "C" {
void startup_early_hook();
}
extern "C" {
#endif
  void startup_early_hook() {
#if 1
    // clock source 0 LPO 1khz, 60 s timeout
    WDOG_TOVALL = 60000; // The next 2 lines sets the time-out value. This is the value that the watchdog timer compare itself to.
    WDOG_TOVALH = 0;
    WDOG_STCTRLH = (WDOG_STCTRLH_ALLOWUPDATE | WDOG_STCTRLH_WDOGEN | WDOG_STCTRLH_WAITEN | WDOG_STCTRLH_STOPEN); // Enable WDG
#else
    // bus clock  60 s timeout
    uint32_t ticks = 60000 * (F_BUS / 1000); // ms
    WDOG_TOVALL = ticks & 0xffff; // The next 2 lines sets the time-out value. This is the value that the watchdog timer compare itself to.
    WDOG_TOVALH = (ticks >> 16) & 0xffff;
    WDOG_STCTRLH = (WDOG_STCTRLH_ALLOWUPDATE | WDOG_STCTRLH_CLKSRC | WDOG_STCTRLH_WDOGEN | WDOG_STCTRLH_WAITEN | WDOG_STCTRLH_STOPEN);
#endif
    WDOG_PRESC = 0; // prescaler
  }
#ifdef __cplusplus
}
#endif

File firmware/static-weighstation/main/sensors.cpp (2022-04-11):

/**
All sensor related functions, including:
Weighstation data, temperature monitoring, power monitoring and payload handling
*/

#include "sensors.h"

// Struct of parameters to store on SD card and send over LoRaWAN 
static parameters_t parameters;

// Weights and timeStamps
static int16_t weights[WeighStation::nScales][WeighStation::maxArrSize];
static int32_t timeStamps[WeighStation::nScales][WeighStation::maxArrSize];

// Setup pin mapping for data and clock lines
static constexpr uint8_t scaleData[WeighStation::nScales] = {4, 21, 30};
static constexpr uint8_t scaleClock[WeighStation::nScales] = {3, 20, 29};

// Overtime check (animal has spent too long on the scales)
static bool overtime[WeighStation::nScales] = {false, false, false};

// Set calibration factor for scale (see calibration script)
static constexpr int16_t calibrationFactors[WeighStation::nScales] = {-1750, -1730, -1730};

// Initalise HX711 library
static HX711 scaleOne;
static HX711 scaleTwo;
static HX711 scaleThree;
// Store HX711 objects in array for easy indexing
static constexpr HX711* scales[WeighStation::nScales] = {&scaleOne, &scaleTwo, &scaleThree};

// Check active scale
static bool scaleActive[WeighStation::nScales] = {false, false, false};

// Note start time (using millis())
static uint32_t weighStartTime[WeighStation::nScales] = {0, 0, 0};

// Position in weights array
static uint16_t readingPos[WeighStation::nScales] = {0, 0, 0};

// Initialse INA219 (power monitoring) library 
static Adafruit_INA219 battery(Monitoring::batteryAddr);
static Adafruit_INA219 solar(Monitoring::solarAddr);

// DallasTemperature (oneWire)
DallasTemperature sensor;

uint32_t unixTime = 1647293354; // Current UNIX time

// Current position in payloads array
uint8_t WeighStation::payloadPos = 0;

// Solar and battery monitoring
bool Monitoring::batteryConnected = false;
bool Monitoring::solarConnected = false;


/**
Initialise the weighstation. 
Set their calibration factors.
Zero them (tare).
*/
void WeighStation::init() {
  Serial.print("[WEIGH STATION]: Initialising");
  for(uint8_t i = 0; i < nScales; i++) {
    scales[i]->begin(scaleData[i], scaleClock[i]);
    scales[i]->set_scale(calibrationFactors[i]);
    scales[i]->tare();
    Serial.print(".");
  }
  Serial.println(" success");
}

/**
Calculate root mean square error of fitted plateau.
@param ts Timestamps.
@param weights Corresponding liveweights.
@param slope The slope of the line.
@param yIntercept The y-intercept of the line.
@returns rmse The root mean square error.
*/
template <size_t SIZE>
float WeighStation::root_mean_sqare_error(int32_t (&ts)[SIZE], int16_t (&weights)[SIZE], 
                                        float slope, float yIntercept){
  float sum = 0.0f;
  for(unsigned int i = 0; i < SIZE; i++){
    float predicted = slope * ts[i] + yIntercept;
    sum += pow(predicted - weights[i], 2);
  }

  float rmse = sqrt(sum / SIZE);
  
  return rmse; 
}

/**
Find areas in the timeseries measurments where the weights plateau, indicating a stable reading.
@param ts Timestamps.
@param weights Corresponding liveweights.
@param inputLength The length of values within weights array that contain values.
@returns fit Of type fit_t, containing fitting parameters from weight readings.
*/
template <size_t SIZE>
fit_t WeighStation::find_plateau(int32_t (&ts)[SIZE], int16_t (&weights)[SIZE], int16_t inputLength){
 
  float slopeBound = 0.10f;
  int16_t maxStableWeight = 0;

  float timeStable = 0.0f;
  float minRmse = 0.0f;
  bool initRmse = false;

  const uint8_t vals = 5;
  for(int16_t i = 0; i < (inputLength - vals); i++){
    
    int32_t x[vals] = {ts[i], ts[i+1], ts[i+2], ts[i+3], ts[i+4]};
    int16_t y[vals] = {weights[i], weights[i+1], weights[i+2], weights[i+3], weights[i+4]};

    // Get slope
    float slope = findSlope(ts[i], ts[i+4], weights[i], weights[i+4]);
    float yIntercept = weights[i] - (slope * ts[i]);

    // Calc root mean square error
    float rmse = WeighStation::root_mean_sqare_error(x, y, slope, yIntercept);

    // Calc average
    int32_t sum = 0;
    for(int z = 0; z < vals; z++){
      sum += y[z];
    }
    int16_t avgWeight = sum / vals;

    // Initialise parameters
    if(!initRmse){
      maxStableWeight = avgWeight;
      timeStable = ts[i];
      minRmse = rmse;
      initRmse = true;
    }

    // Replace parameters if a better fit is found
    if(abs(slope) < slopeBound && avgWeight >= maxStableWeight && rmse < minRmse){
      maxStableWeight = avgWeight;
      timeStable = ts[i];
      minRmse = rmse;
    }

  }

  fit_t fit;
  fit.maxStableWeight = maxStableWeight;
  fit.timeStable = timeStable;
  fit.rmse = minRmse;

  #ifdef DEBUG
    Serial.print("Max Stable Weight: ");
    Serial.print(fit.maxStableWeight / 100.0f);
    Serial.print(" kg p.m. ");
    Serial.print(fit.rmse  / 100.0f);
    Serial.print(" kg at: ");
    Serial.print(fit.timeStable  / 1000.0f);
    Serial.println("s");
  #endif // DEBUG

  return fit;
}


/**
Reset all scales to zero (tare weight).
Call often as scales drift over time.
*/
void WeighStation::tare_scales() {
  #ifdef DEBUG
    Serial.println("[WEIGH STATION]: Tare scales.");
  #endif
  for(uint8_t i = 0; i < nScales; i++) {
    scales[i]->tare(); // Reset to zero
  }
}


/**
Power down ADC's (HX711) when in sleep mode.
*/
void WeighStation::sleep() {
  for(uint8_t i = 0; i < nScales; i++) {
    scales[i]->power_down();
  }
}


/**
Power up ADC's (HX711) when coming out of sleep mode.
*/
void WeighStation::wakeup() {
  for(uint8_t i = 0; i < nScales; i++) {
    scales[i]->power_up();
  }
}
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

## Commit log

2021-04-30 inital commit
    [UniversalNode.kicad_pcb, UniversalNode.sch]
2021-05-27 update firmware
    [UniversalNode.sch]
2021-06-15 added v0.2
    [UniversalNode.kicad_pcb, UniversalNode.sch]
2021-06-16 finalising version 0.2
    [UniversalNode.kicad_pcb, UniversalNode.sch]
2021-06-18 finalised v0.2
    [UniversalNode.kicad_pcb, UniversalNode.sch]
2021-06-21 added atmega lora module
    [UniversalNode.kicad_pcb, UniversalNode.sch]
2021-06-24 working arduino pro mini LoRaWAN
2021-07-01 atmega328 needs RX <-> TX swap, button leads chopped, but LoRaWAN and SD Card working
    [main.ino]
2021-07-06 trying to optimise for atmega328
    [UniversalNode.sch]
2021-07-07 atmega scale and lora, teensy sleep mode with lora clean wake up
2021-07-07 added v0.3
    [UniversalNode.kicad_pcb, UniversalNode.sch]
2021-07-08 updated v0.3 and sent for production
    [UniversalNode.kicad_pcb]
2021-07-16 updated v0.3 with interactive BOM
2021-07-19 teensy and atmega328 talking bytes
    [UniversalNode.sch]
2021-07-20 working interrupt teensy atmega328
2021-07-23 i2c, coms, memory working for teesny
2021-07-26 added interrupt disabling during measurment
    [UniversalNode.sch]
2021-07-29 modified 9v resistor divider
    [UniversalNode.sch]
2021-08-02 updated teensy side
2021-08-04 updated sleep config (19 mA with 4 mc's
2021-08-05 updated teensy for depolyment
2021-08-06 added calibration sketch
2021-08-16 updated for v0.4 and added additional schematic parts
    [AOD417.step, BH32T-C-G.step, BK-18650-PC2.step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]
2021-08-25 update v0.3 with weigh scale trigger fix
    [lora.cpp, main.ino, memory.cpp]
2021-09-09 rm and update
    [UniversalNode.kicad_pcb]
2021-09-09 need to fix drink time for v0.4
    [lora.cpp, main.ino, memory.cpp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]
2021-09-10 working on v0.4, temperature needs work
2021-09-17 fixed power monitoring in v0.4
    [main.ino, sensors.cpp]
2021-11-14 added version 0.4.2 and 0.5
    [BatteryHolder.kicad_pcb, TSR_1-2450.step, UniversalNode.kicad_pcb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]
2021-11-25 added ibom for v0.5
    [UniversalNode.kicad_pcb]
2021-12-14 potenital fix for random device stoppage
    [sensors.cpp]
2021-12-17 added watchdog timer
    [AOD417.step, BH32T-C-G.step, BK-18650-PC2.step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]
2021-12-19 added overtime (too long on scales) fix (hopefully)
    [main.ino, sensors.cpp]
2021-12-20 updated some functions that could fail?
    [lora.cpp, main.ino, sensors.cpp]
2021-12-21 added payload position checking and changed error in check_state()
    [sensors.cpp]
2021-12-22 added estimated weight function (need to change decoder)
    [weighscale_test.xlsx]
2021-12-22 updated folder structure
    [AOD417.step, BH32T-C-G.step, BK-18650-PC2.step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]
2022-01-11 added citation.cff file
    [UniversalNode.sch]
2022-01-13 cleaned and added docs
    [BatteryHolder.kicad_pcb, UniversalNode.kicad_pcb, UniversalNode.sch]
2022-01-24 updated with calibration data
2022-02-14 added arduino shield
    [TXB0104D.step, UniversalNode.kicad_pcb, UniversalNode.sch]
2022-04-12 prepared final figures (schematic and pcb) for sup material
    [UniversalNode.kicad_pcb, UniversalNode.sch]
2023-01-09 removed arduino shield project and re-added .lib files for kicad components
    [UniversalNode.kicad_pcb, UniversalNode.sch]
